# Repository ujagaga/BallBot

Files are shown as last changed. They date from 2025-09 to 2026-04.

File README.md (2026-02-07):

# BallBot

An arduino robot to collect PingPong balls. It contains: 
1. ESP32 Cam module to provide optical info and WiFi controllabillity
2. 3 servo motors (9g servo) for ball claws, head (ESP32 cam) and drive wheel direction rotation
3. Brushless DC motor as the main drive wheel (Gimbal Brushless Motor for Gopro 808) 
4. Brushless motor driver
5. Li-Ion battery 3.7V (2 x 18650 in parallel)
6. 2 nickel strips on the bottom of the battery pack as charging rails
7. Li-Ion charger module with battery protection and 5V boost module to power the ESP32 Cam module
8. DC/DC boost module to raise the battery voltage to 6V for the BLDC motor driver and to power the servo motors

The casing is 3D printed using cheapest PLA.
The screws are 1mm x 10mm. If you are building your own please edit the 3D model to support what ever screws you are using.
The screw holles are made smaller and screws are heated using a soldering iron before they were screwd in, to melt the plastic and create threads.

## Server

1. ESP32 CAM configured as a WiFi access point or station. You can choose on initialization of WiFi
2. ESP32 runs an HTTP server to provide video stream, manual control and API access

## Building the firmware

Generally you can use the Arduino IDE and in Preferences add the ESP32 board manager.
```
https://raw.githubusercontent.com/espressif/arduino-esp32/gh-pages/package_esp32_index.json
```
After that you can select the ESP32 Cam board and build the firmware. I also provided scripts that can build and upload the firmware via USB. You can find them at:

        tools/build_firmware.sh
        tools/upload_firmware.sh

I prefer using the VS Code or Antigravity to Arduino IDE, so all you need is to install the C/C++ extension and then ask the AI to set up the build environment for you, so it can find the correct libraries and provide the code complete and prediction.

## Updating ESP32 firmware via WiFi
There is an /api/ota endpoint to which you need to make a post request to trigger the update. Basically you need to serve the image file and then trigger the update by sending the url where the image can be downloaded. I provided a python script to simplify this at:

        tools/update_firmware.py

The only requirement is `pip install requests`

The partition scheme you will need is one with OTA. Just in case you need it, you can find it at:

        tools/partitions.csv

You only need to upload the image once via USB to adjust the partition scheme. After that you can use the WiFi update mechanism which only sends the application image to the ESP32, so the partition scheme needs to be correctly pre-defined and will not be changed by the WiFi upload process.

## WARNING
The WiFi AP causes a lot of electrical noise, so the camera tends to freeze due to processing errors. To prevent it, make sure you have a module with an antenna, which you place on the side, behind the camera and glue the camera to the SD card slot to allow it to shield it.

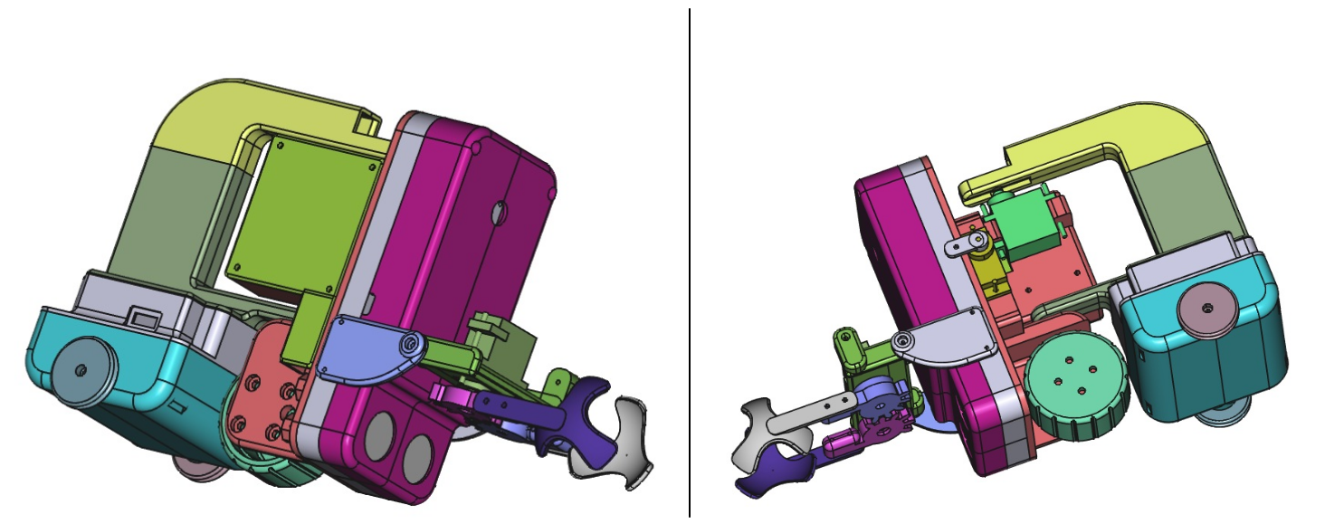
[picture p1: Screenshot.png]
3D Preview


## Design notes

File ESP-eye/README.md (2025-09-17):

# ESP 32 Eye #

I made this for my robot to be able to stream video so I can process it remotelly.

## How to start ##

1. Copy "config.h.example" to "config.h" and adjust your credentials. This is to avoid posting my credentials to git.

2. Open Arduino IDE and install support for ESP32. Go to "Arduino > Preferences" and enter: 

        https://raw.githubusercontent.com/espressif/arduino-esp32/gh-pages/package_esp32_index.json 

into the “Additional Board Manager URLs” field

3. Go to "Tools > Board > Boards Manager" and search for "esp32" Install "esp32 by Espressif Systems" and "Arduino ESP32 Boards"

4. Go to "Sketch > Include Library > manage Libraries" and install "ArduinoOTA"

5. Connect your ESP32-cam board, select it in the boards manager and program it.

6. Open the Serial Monitor to view debugging messages to see which IP it serves on, so you can find it in your web browser.

7. Use a better 5V power supply than your computer USB port for better video quality.

## Contact ##

* web: http://www.radinaradionica.com
* email: ujagaga@gmail.com

## ESP32 Pinout
Label  	GPIO  	Use			Reason
D0	0	Sens Trig 10K to Vcc	must be HIGH during boot and LOW for flashing
TX0	1	No			Tx pin, used for flashing and debugging
D2	2	Direction 10K to GND	must be LOW during boot
RX0	3	No			Rx pin, used for flashing and debugging
D4	4	Speed			Connected to the on-board Flash LED
D12	12	Servo 1			must be LOW during boot
D13	13	Servo 2
D14	14	Servo 3
D15	15	No			must be HIGH during boot, prevents startup log if pulled LOW
RX2	16	Sens Echo

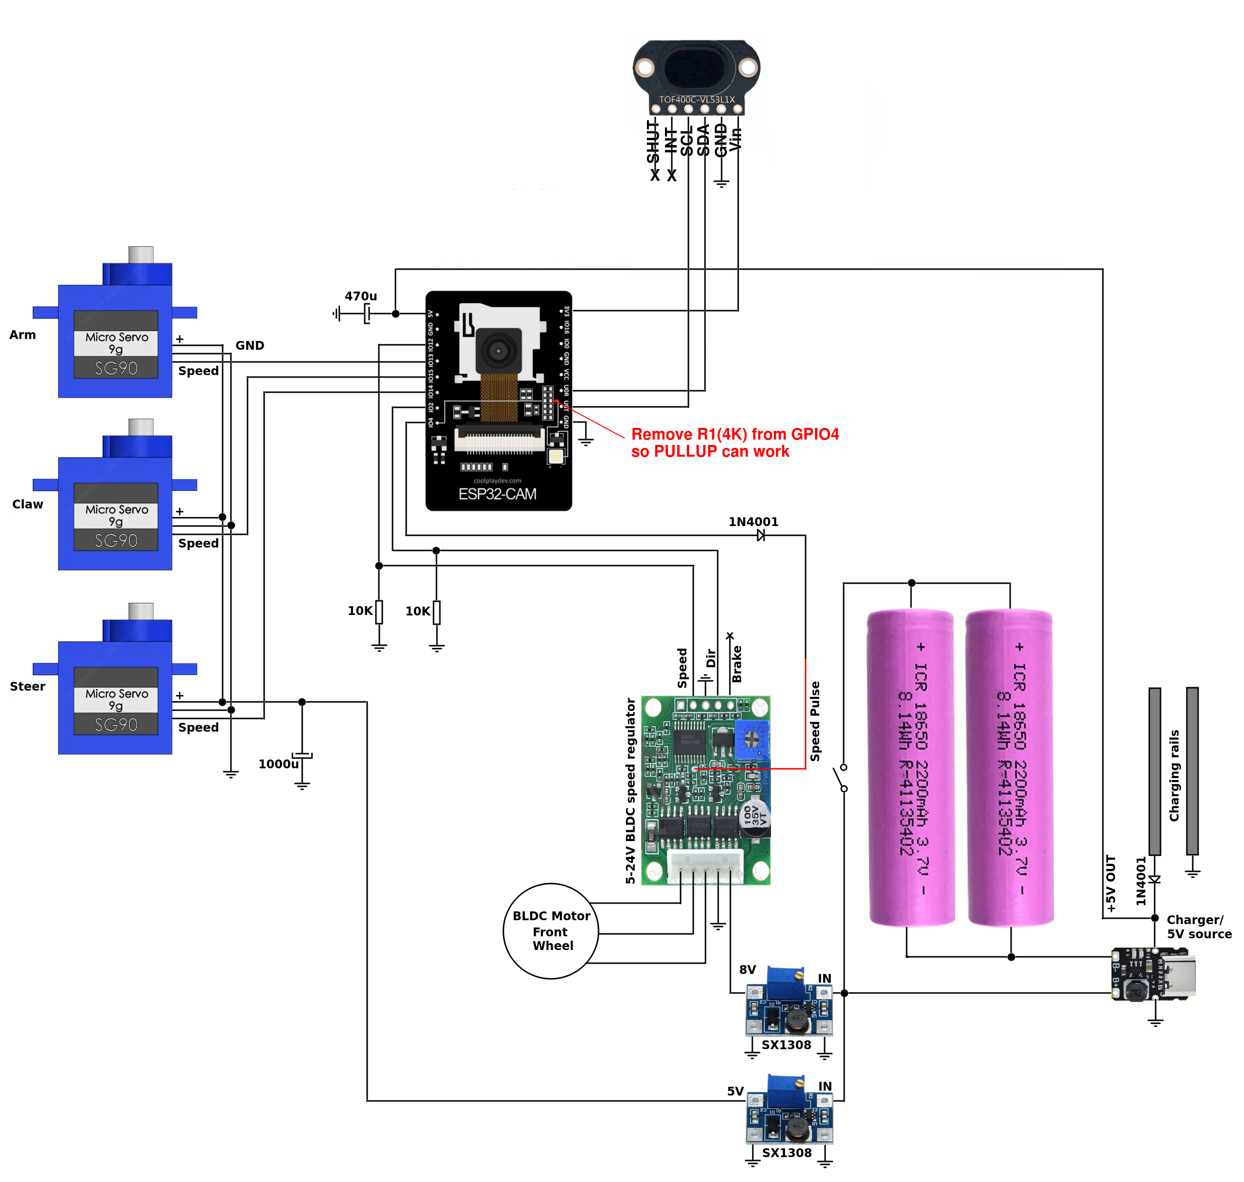
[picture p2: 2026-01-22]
Robot_schematic.png

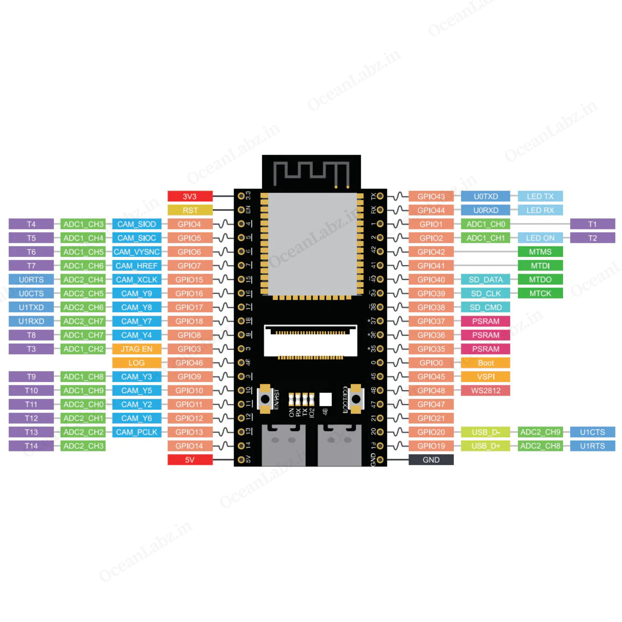
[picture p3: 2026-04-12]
pinout-image-4.png.webp

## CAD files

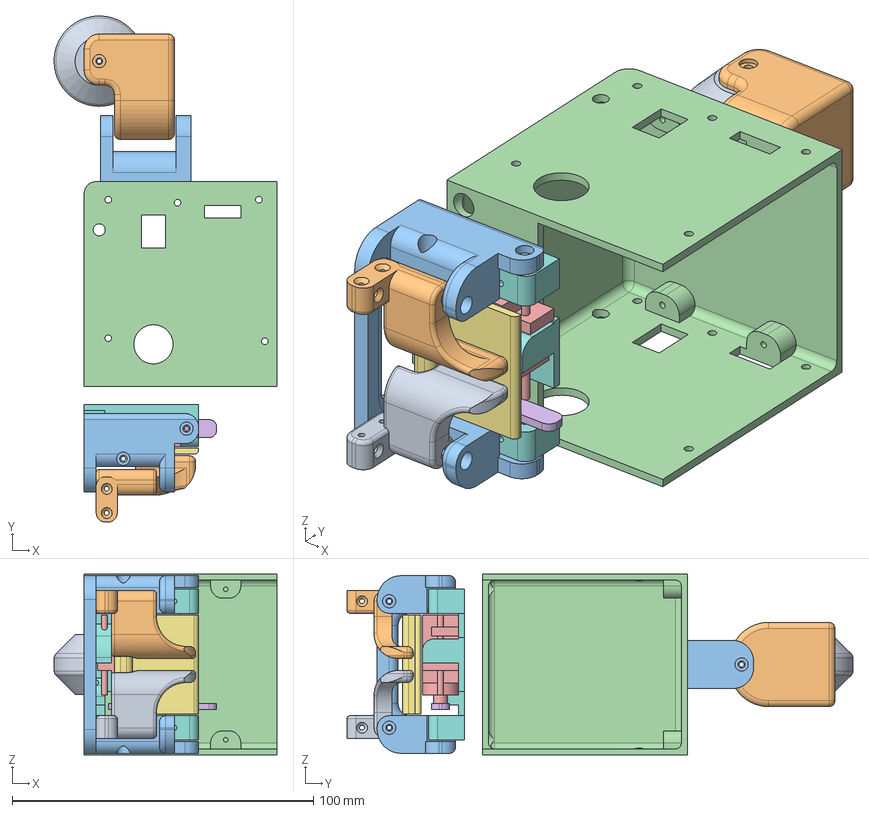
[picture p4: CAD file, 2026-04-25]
3d_models/BallBot2.FCStd
74.0 x 168.0 x 60.0 mm
RearWheel
WheelFork
RearWheelHindge
PcbBox
ClawServo
Winch001
Hindge002
HindgeBase
Arm001
Arm002
Hindge001

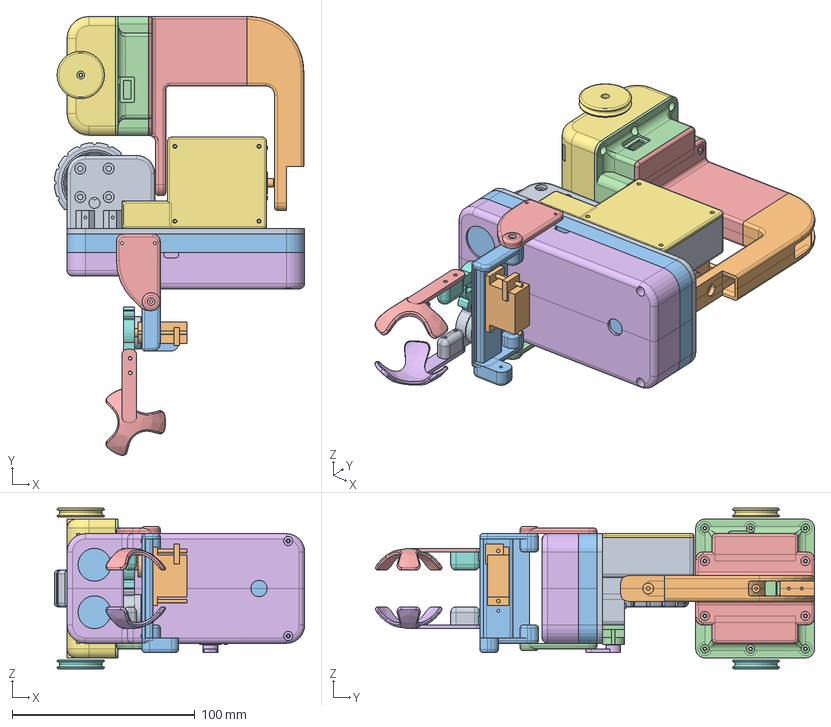
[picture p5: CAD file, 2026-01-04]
3d_models/BallBot.FCStd
137.0 x 240.2 x 88.0 mm
FrontTire
MainWheelServo
Sensor
ArmServo001
ClawRight
ClawLeft
RearWheel001
RearWheel002
MainBoard
SpineTop
PcbHolder
ArmHolder
ArmHolder (Mirror #7)
ArmWinch
Cover001
MotorArmGear001
SlaveArmGear
ClawServo
ArmServoPlate
BatBoxMiddle
Spine
Cover
BatteryBox

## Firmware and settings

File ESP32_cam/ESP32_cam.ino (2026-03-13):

#include "camera.h"
#include "distance.h"
#include "http_client.h"
#include "http_server.h"
#include "motor.h"
#include "wifi_connection.h"

void setup() {
  DISTANCE_init();
  MOTOR_init();
  CAM_Init();
  WIFIC_init(true);
  HTTPSRV_init();
  CAM_preset();
}

void loop() {
  if (!HTTPC_fwUpdateInProgress()) {
    MOTOR_process();
  }
  HTTPC_process();

  delay(50); // less than 40 will freeze the camera
}

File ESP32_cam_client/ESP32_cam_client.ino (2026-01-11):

// ESP32_cam_client.ino
#include <WiFi.h>
#include "tcp_client.h"
#include "camera.h"
#include "wifi_connection.h"
#include "motor.h"
#include "distance.h"
#include "http_client.h"

static bool connected = false;

void setup() { 
  WIFIC_init();  
  MOTOR_init();
  DISTANCE_init();  
  CAM_Init();   
}

void loop() {  
  TCPC_Process(); 
  if(!TCPC_IsFwUpdateInProgress()){
    MOTOR_process(); 
  }  
}

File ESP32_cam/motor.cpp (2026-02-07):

#include "motor.h"
#include "logger.h"
#include <Arduino.h>

// ======================================================
// ==================== STATE ============================
// ======================================================

static uint32_t lastServoUpdate = 0;
static uint32_t cmdTimeOut = 0;
const uint16_t SERVO_UPDATE_MS = 20;
volatile uint32_t wheel_pulses = 0;

enum GrabState { IDLE, OPENING_CLAW, LOWERING_ARM, GRABBING, RAISING_ARM };

GrabState grabState = IDLE;

// ---------------- Servo ----------------

struct ServoMotor {
  uint8_t currentAngle;
  uint8_t targetAngle;
  uint8_t increment;
  uint8_t pin;
};

static ServoMotor mSteer;
static ServoMotor mClaw;
static ServoMotor mArm;

// ---------------- Distance move ----------------

struct DistanceMove {
  uint32_t targetPulses;
  uint32_t lastProcessedPuls;
  int speed;
  bool keepDir;
  bool active;
};

static DistanceMove currentMove;

// ======================================================
// ==================== UTIL =============================
// ======================================================

static inline uint32_t angleToDuty(uint8_t angle) {
  uint32_t us = map(angle, 0, 180, SERVO_MIN_US, SERVO_MAX_US);
  uint32_t maxDuty = (1UL << SERVO_PWM_RES) - 1;
  return (us * maxDuty) / (1000000UL / SERVO_PWM_FREQ);
}

static inline void servoWrite(const ServoMotor &m) {
  ledcWrite(m.pin, angleToDuty(m.currentAngle));
}

uint32_t get_pulses() {
  noInterrupts();
  uint32_t p = wheel_pulses;
  interrupts();
  return p;
}

static inline uint8_t clamp(int v, int minv, int maxv) {
  if (v < minv)
    return minv;
  if (v > maxv)
    return maxv;
  return (uint8_t)v;
}

// ======================================================
// ==================== ISR ==============================
// ======================================================

void IRAM_ATTR wheel_isr() { wheel_pulses++; }

// ======================================================
// ==================== INIT =============================
// ======================================================

static void servoInit(ServoMotor &m, uint8_t startAngle, uint8_t speed,
                      uint8_t pin, uint8_t channel) {
  m.currentAngle = startAngle;
  m.targetAngle = startAngle;
  m.increment = speed;
  m.pin = pin;

  // Attach hardware PWM to pin with explicit channel
  ledcAttachChannel(pin, SERVO_PWM_FREQ, SERVO_PWM_RES, channel);
  servoWrite(m);
}

void MOTOR_setTimeout(uint32_t timeToSet) { cmdTimeOut = timeToSet; }

void MOTOR_init() {

  // ---- Servos ----
  // Use channels 4-6 to avoid camera's LEDC_CHANNEL_0
  servoInit(mSteer, 90, SERVO_STEER_SPEED, SERVO_STEER_PIN, 4);
  servoInit(mClaw, 90, SERVO_CLAW_SPEED, SERVO_CLAW_PIN, 5);
  servoInit(mArm, 90, SERVO_ARM_SPEED, SERVO_ARM_PIN, 6);

  // ---- BLDC direction ----
  pinMode(BLDC_DIR_PIN, OUTPUT);
  digitalWrite(BLDC_DIR_PIN, LOW);

  // ---- BLDC PWM ----
  // Use channel 7 to avoid camera's LEDC_CHANNEL_0
  ledcAttachChannel(BLDC_SPEED_PIN, BLDC_PWM_FREQ, BLDC_PWM_RES, 7);
  ledcWrite(BLDC_SPEED_PIN, 0);

  // ---- Tacho ---- Does not work
  pinMode(BLDC_TAHO_PIN, INPUT_PULLUP);
  attachInterrupt(digitalPinToInterrupt(BLDC_TAHO_PIN), wheel_isr, FALLING);
}

// ======================================================
// ==================== SERVO API ========================
// ======================================================

void MOTOR_setSteerServo(int a) {
  mSteer.targetAngle = clamp(a, SERVO_STEER_MIN, SERVO_STEER_MAX);
}
void MOTOR_setArmServo(int a) {
  mArm.targetAngle = clamp(a, SERVO_ARM_MIN, SERVO_ARM_MAX);
}
void MOTOR_setClawServo(int a) {
  mClaw.targetAngle = clamp(a, SERVO_CLAW_MIN, SERVO_CLAW_MAX);
}

void MOTOR_incrementSteerServo(int d) {
  MOTOR_setSteerServo(mSteer.targetAngle + d);
}
void MOTOR_incrementArmServo(int d) { MOTOR_setArmServo(mArm.targetAngle + d); }
void MOTOR_incrementClawServo(int d) {
  MOTOR_setClawServo(mClaw.targetAngle + d);
}

void MOTOR_grabBall() { grabState = OPENING_CLAW; }

void MOTOR_releaseBall() { MOTOR_setClawServo(SERVO_CLAW_MAX); }

// ======================================================
// ==================== BLDC =============================
// ======================================================

static void moveBldc(int speed) {

  bool forward = speed >= 0;
  digitalWrite(BLDC_DIR_PIN, forward);

  uint32_t duty = abs(speed);
  if (duty > 1023)
    duty = 1023;

  ledcWrite(BLDC_SPEED_PIN, duty);
}

void MOTOR_moveToDistance(uint32_t pulses, int speed, bool keepDirection) {
  noInterrupts();
  wheel_pulses = 0;
  interrupts();

  currentMove.targetPulses = pulses;
  currentMove.lastProcessedPuls = 0;
  currentMove.speed = speed;
  currentMove.keepDir = keepDirection;
  currentMove.active = true;

  moveBldc(speed);
}

void MOTOR_stopAll() {
  mSteer.targetAngle = mSteer.currentAngle;
  mArm.targetAngle = mArm.currentAngle;
  mClaw.targetAngle = mClaw.currentAngle;
  servoWrite(mSteer);
  servoWrite(mArm);
  servoWrite(mClaw);
  moveBldc(0);
  currentMove.active = false;
}

// ======================================================
// ==================== PROCESS ==========================
// ======================================================

static void processServo(ServoMotor &m, int minA, int maxA) {

  int delta = m.targetAngle - m.currentAngle;
  if (!delta)
    return;

  int step = min(abs(delta), (int)m.increment);
  m.currentAngle += (delta > 0) ? step : -step;
  m.currentAngle = clamp(m.currentAngle, minA, maxA);

  servoWrite(m);
}
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

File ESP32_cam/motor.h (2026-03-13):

#pragma once

#include <stdint.h>
#define SERVO_STEER_PIN (21)
#define SERVO_CLAW_PIN (38)
#define SERVO_ARM_PIN (47)
#define BLDC_SPEED_PIN (14)
#define BLDC_DIR_PIN (2)
#define BLDC_TAHO_PIN (48)

#define SERVO_STEER_SPEED (3)
#define SERVO_CLAW_SPEED (5)
#define SERVO_ARM_SPEED (6)

#define SERVO_STEER_MIN (12)
#define SERVO_STEER_MAX (160)
#define SERVO_CLAW_MIN (83)
#define SERVO_CLAW_MAX (105)
#define SERVO_ARM_MIN (45)
#define SERVO_ARM_MAX (140)

#define STEERING_STRAIGHT_ANGLE (85)
#define STEERING_PER_PULSE (20)

#define SERVO_PWM_FREQ (50)
#define SERVO_PWM_RES (16)
#define SERVO_MIN_US (500)
#define SERVO_MAX_US (2500)

// ---- BLDC PWM ----
#define BLDC_PWM_FREQ (20000)
#define BLDC_PWM_RES (10)

#define MOTOR_TIMEOUT (1000)

extern void MOTOR_init(void);
extern void MOTOR_setSteerServo(int angle);
extern void MOTOR_setArmServo(int angle);
extern void MOTOR_setClawServo(int angle);
extern void MOTOR_incrementSteerServo(int angle);
extern void MOTOR_incrementArmServo(int angle);
extern void MOTOR_incrementClawServo(int angle);
extern void MOTOR_stopAll(void);
extern void MOTOR_process(void);
extern void MOTOR_setTimeout(uint32_t timeToSet);
extern void MOTOR_moveToDistance(uint32_t pulses, int speed,
                                 bool keepDirection);
extern void MOTOR_grabBall(void);

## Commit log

2025-01-18 adding new version
    [BallBot1.FCStd, BallBot2.FCStd, WheelDrive.FCStd]
2025-01-21 New version
    [BallBot.FCStd, BallBot1.FCStd, BallBot2.FCStd]
2025-01-26 Final 3D model
    [BallBot.FCStd]
2025-09-16 Add ESP_Eye
    [partitions.csv]
2025-09-18 Updated schematic
    [BallBot.FCStd]
2025-09-20 Update to ESP32 code
2025-09-21 Stopping on socket timeout
2026-01-05 Add switch
2026-01-07 Updated ESP32 code
2026-01-07 Switched commands to json format
2026-01-11 implemented correct firmware update
    [ESP32_cam_client.ino]
2026-02-03 Working version
    [partitions.csv]
2026-02-07 Switched to websockets for motor controlls
2026-03-13 Working ESP32S3 CAM
